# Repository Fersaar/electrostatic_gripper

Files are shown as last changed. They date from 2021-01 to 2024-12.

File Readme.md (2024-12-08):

# Electrostatic gripper

This project was developed as part of my academic studies, with the objective of creating a gripper specifically designed for handling thin lithium foil (less than 20 micrometers). Lithium is a highly reactive and sensitive material, which presents challenges when it comes to handling. Traditional methods, such as pneumatic grippers and large-area suction pads commonly used in film handling, are problematic because they would require the use of inert gas as the process medium. Additionally, pneumatic systems pose a risk of contaminating the foil with particles from the environment. As a result, electrostatic grippers offer a viable solution.

## Functional principle

The underlying principle of the electrostatic gripper is that opposite electrical charges attract each other. When a voltage is applied to two parallel plates, an attractive force is generated between them (similar to the forces in a capacitor). Furthermore, a centering force is produced when the two plates are moved relative to one another.
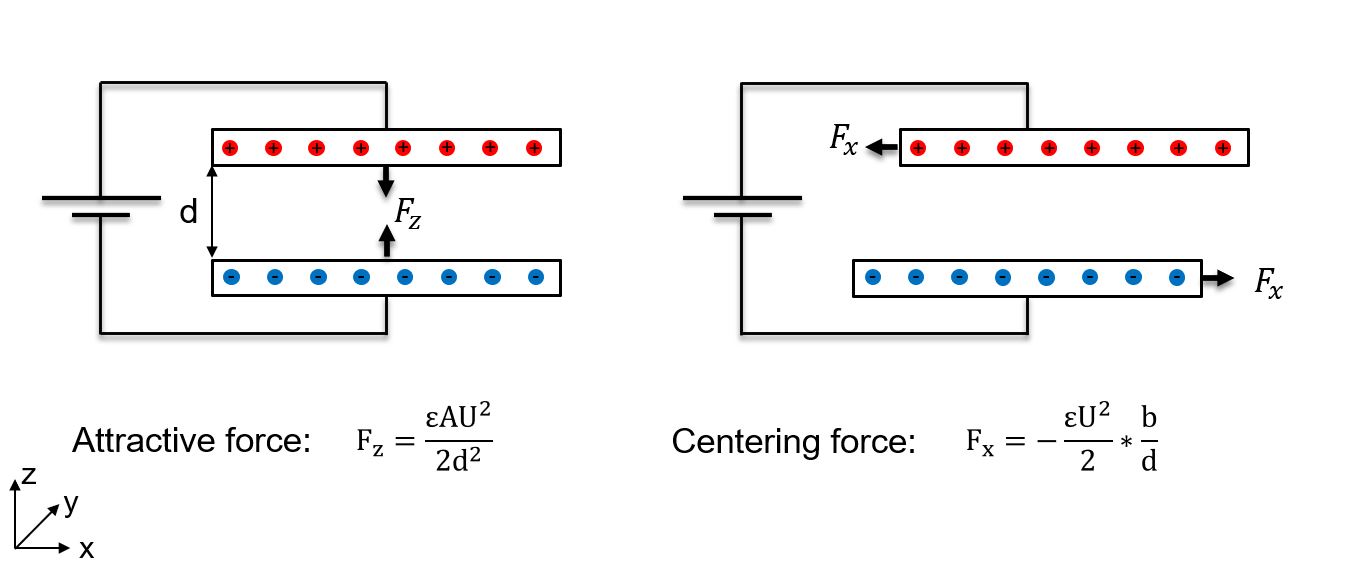
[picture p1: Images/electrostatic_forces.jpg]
electrostatic forces


## Gripper designs

Based on this principle, various gripper designs can be developed. The simplest design, known as the monopolar gripper, operates on the concept of two parallel plates. In this configuration, one plate is formed by the gripper, while the second plate is represented by the foil being handled. A voltage is applied between the gripper and the foil.

In contrast, the bipolar design consists of two electrodes between which a voltage is applied. This setup induces movement in the electrically conductive foil. The gripper and the foil together form two capacitors connected in series. One advantage of this design is that the foil does not need to be electrically contacted or charged. However, the maximum achievable force is reduced by half, as the applied voltage is divided between the two capacitors.

Furthermore, the bipolar design allows for the handling of non-conductive materials, such as paper. In this case, the force is generated through polarization rather than charge displacement. The individual molecules within the material align themselves with the electrostatic field produced by the gripper, forming dipoles. The force achievable with this method is lower than with conductive materials. Therefore, a strong electric field is particularly important, making an interdigitated design preferable. The reduced distance between opposing electrodes results in a higher electric field strength.

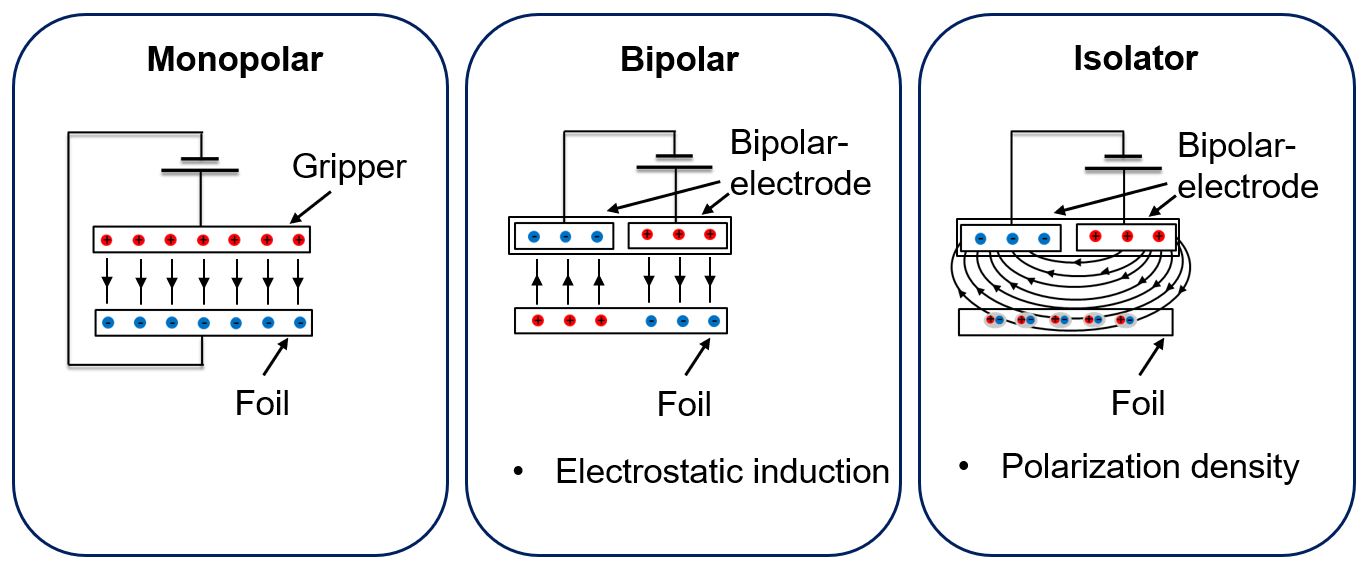
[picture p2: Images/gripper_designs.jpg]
gripper design


## Gripper

The gripper consists of two copper electrodes, each with an area of 70 x 35mm. The insulation distance between the two surfaces is 1 to 2 mm. A voltage of 1000 V is applied between the two electrodes.
| | |
|--|---|
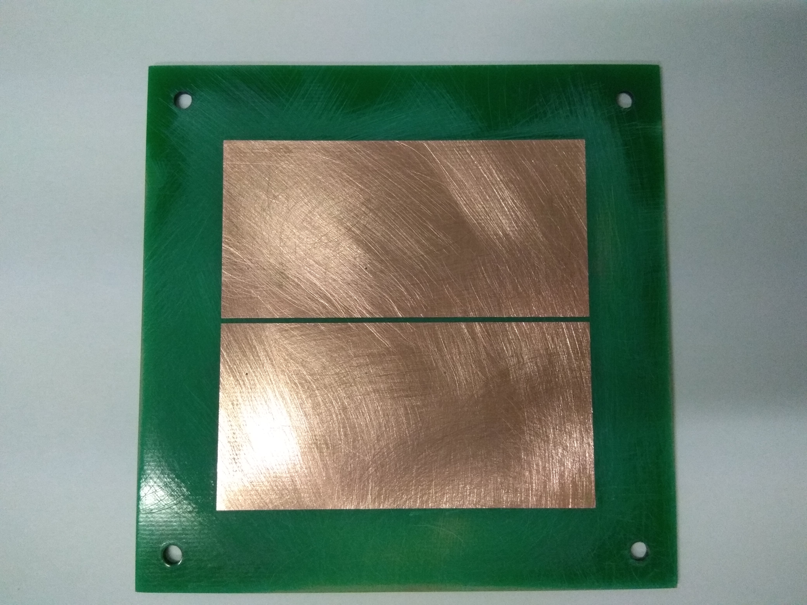
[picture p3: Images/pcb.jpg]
pcb
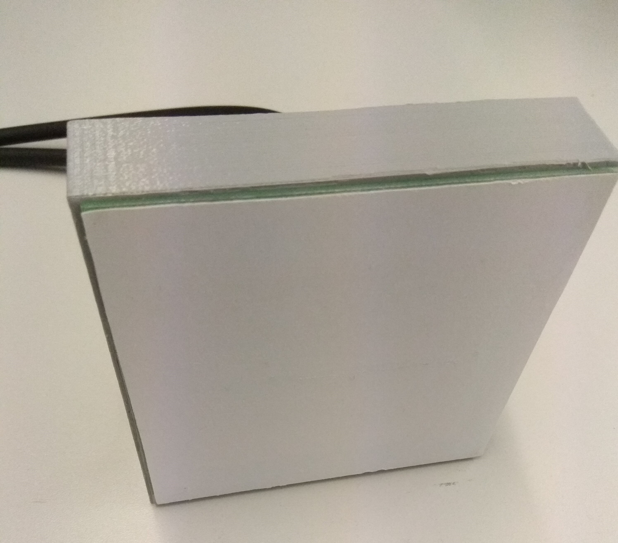
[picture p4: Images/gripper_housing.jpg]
Gripper
| | |
|gripper/board | gripper with housing and insulation |

<br />
To prevent the electrically conductive lithium foil from short-circuiting the two electrodes during handling, it is essential to insulate them. However, this presents a challenge: the insulation material is subjected to the electric field, which causes it to become polarized and generate its own electric field. When the gripper is turned off, the polarization of the insulation material dissipates slowly, and the electric field it produces continues to hold the film to the gripper. Therefore, the insulation material must have low polarizability to allow for the quick deactivation of the gripper or the rapid release of the film. The [permittivity](https://de.wikipedia.org/wiki/Permittivit%C3%A4t) can serve as an indicator of the material's polarization capability; the lower the permittivity value, the less polarizable the material is.

Based on these findings, various materials were tested, and different disconnection strategies were explored. In addition to disconnecting the two electrodes from the power supply, the electrodes were switched to either a negative or positive state for shutdown. It was determined that lightly roughened paper was the most suitable material when combined with short-circuiting the two electrodes through the negative terminal of the power supply. This approach allowed for a switch-off time of less than one second.

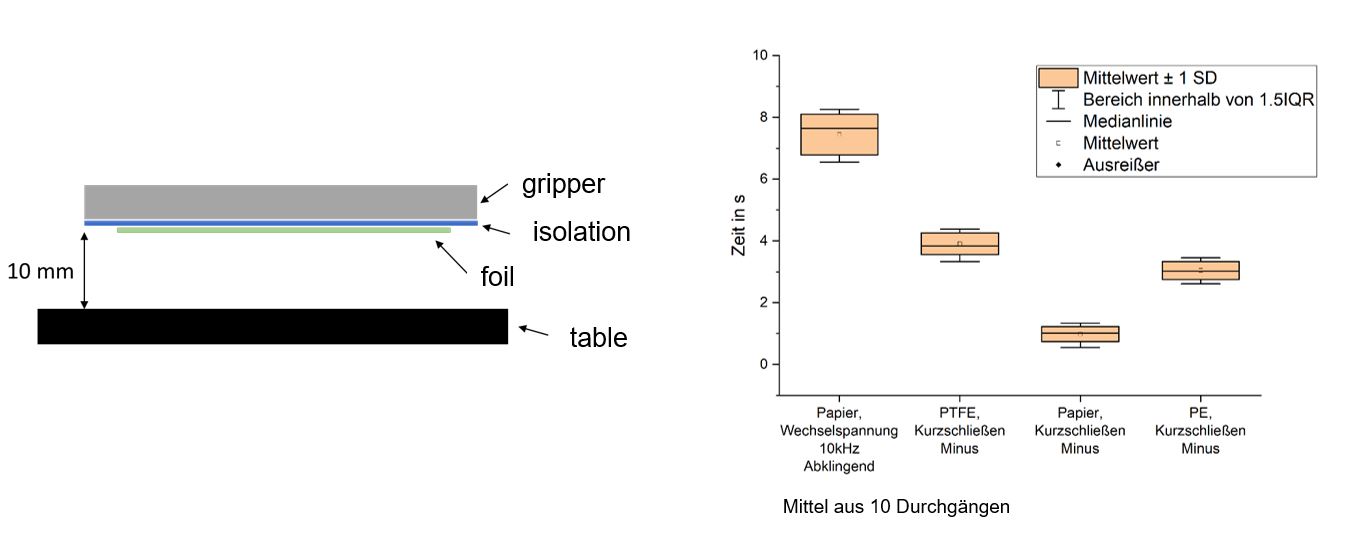
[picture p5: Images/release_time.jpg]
release_time

*Release times with different insulation materials and shutdown methods*

## Practice

With a total electrode area of 70 x 70 mm, a maximum force of 0.35 N was achieved, which is approximately equivalent to 35 grams.

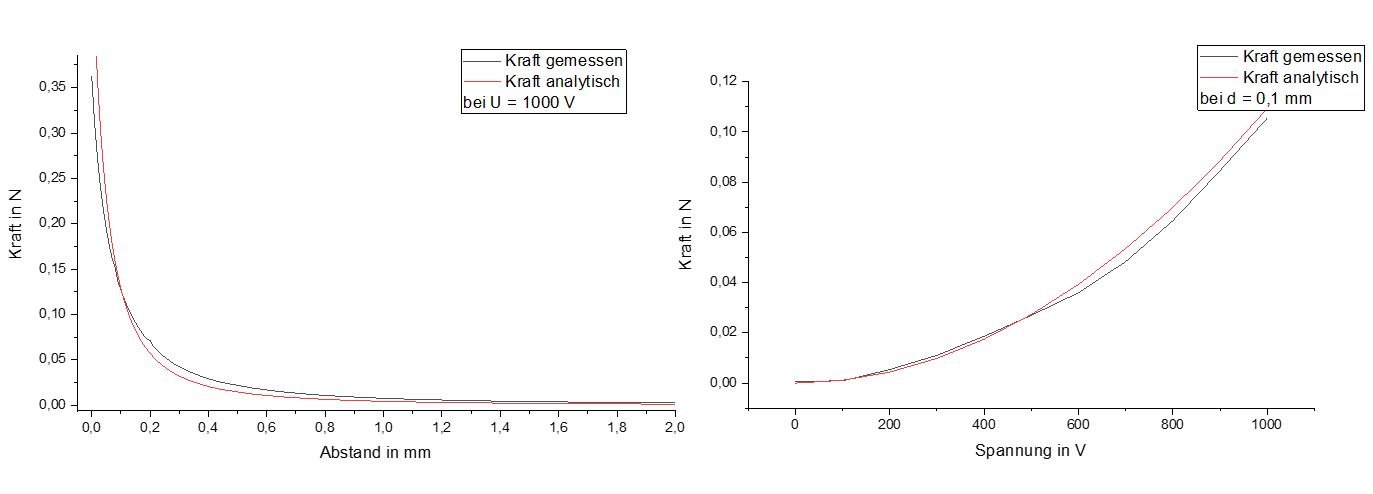
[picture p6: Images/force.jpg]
force


The practical application was successful:

**Video:**

Handling (http://www.youtube.com/watch?v=Acb63k8iqSQ "Handling")

Interdigitaldesign for e.g. paper: 
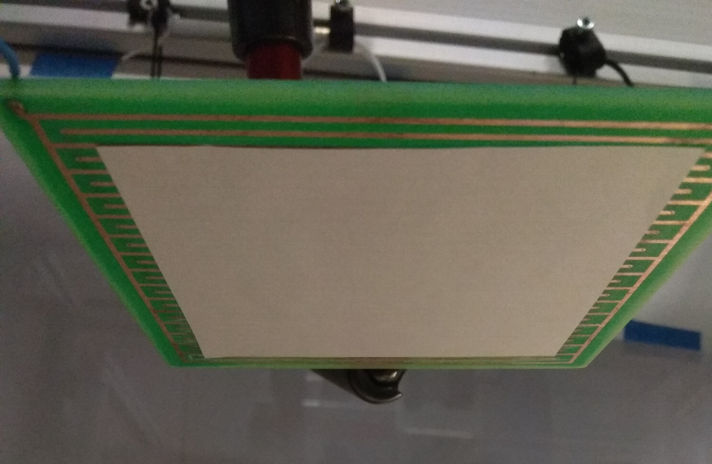
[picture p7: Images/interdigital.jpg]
Interdigital
